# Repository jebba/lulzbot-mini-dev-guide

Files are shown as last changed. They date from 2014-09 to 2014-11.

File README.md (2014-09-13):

# LulzBot Mini Developers Guide

[LulzBot Mini Developers Guide PDF](mini-dev.pdf)

The [LulzBot Mini](http://devel.lulzbot.com/mini/) is a Desktop 3D Printer
currently under development by
[Aleph Objects, Inc.](http://www.alephobjects.com/)

This guide is meant for developers working on the printer or others interested
in learning more about how the machine operates.

Users should see the separate (forthcoming) LulzBot Mini User Manual.

The Guide is written in LaTeX.

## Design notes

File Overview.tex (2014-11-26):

%
% Introduction.tex
%
% LulzBot Mini Developer's Guide
%
% Copyright (C) 2014 Aleph Objects, Inc.
%
% This document is licensed under the Creative Commons Attribution 4.0
% International Public License (CC BY-SA 4.0) by Aleph Objects, Inc.
%

\section{LulzBot Mini}
The LulzBot Mini is a 3D Printer currently under development. The
abbreviated name is mini-dev.

The source files are available here:

\href{http://devel.lulzbot.com/mini/}{http://devel.lulzbot.com/mini/}

\section{Versions}
Each new version of the mini-dev has a new name, with the next letter in the alphabet.

\begin{itemize}
  \item Azalea - First Prototype
  \item Begonia - Second Prototype, being built now
  \item Camellia - Third Prototype
  \item Croton - Fourth Prototype
  \item Daffodil - First Production batch
\end{itemize}

\section{Schedule}
The schedule is updated weekly. It is in Libre Office spreadsheet format. The
latest version is available here:

\url{http://devel.lulzbot.com/mini/program_management/}

\includepdf[addtolist={1,figure,{Work Breakdown Schedule},wbs},pages=-,landscape=true,reflect=false,turn=true,fitpaper=true,keepaspectratio=true]{pm/wbs30.pdf}

\includepdf[addtolist={1,figure,{Phase Gate Schedule},pgs},pages=-,landscape=true,reflect=false,turn=true,fitpaper=true,keepaspectratio=true]{pm/phase-gate-schedule31.pdf}

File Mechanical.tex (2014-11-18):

%
% Mechanical.tex
% Mechanical Development
%
% LulzBot Mini Developer's Guide
%
% Copyright (C) 2014 Aleph Objects, Inc.
%
% This document is licensed under the Creative Commons Attribution 4.0
% International Public License (CC BY-SA 4.0) by Aleph Objects, Inc.
%

\section{Intro}
Mechanical hardware specs and parts are in these subdirectories:

\url{http://devel.lulzbot.com/mini/}

\section{Bill of Materials}

% pdfjam  --papersize '{24.58cm,18.90cm}'   --no-landscape daffodil_bom.pdf '1-3'
\includepdf[addtolist={1,figure,{Bill of Materials},bom},pages=-,landscape=true,reflect=false,turn=false,fitpaper=true,keepaspectratio=true]{bom.pdf}

\section{Drawings}
\includepdf[addtolist={1,figure,{Electronics Case},eleccase},pages=-,landscape=true,reflect=false,turn=false,fitpaper=true,keepaspectratio=true]{PP-FP0056rC.pdf}
\includepdf[addtolist={1,figure,{Top Plate},topplate},pages=-,landscape=true,reflect=false,turn=false,fitpaper=true,keepaspectratio=true]{PP-FP0051rA.pdf}
\includepdf[addtolist={1,figure,{Bottom Plate},bottomplate},pages=-,landscape=true,reflect=false,turn=false,fitpaper=true,keepaspectratio=true]{PP-FP0053rA.pdf}
\includepdf[addtolist={1,figure,{Left Plate},leftplate},pages=-,landscape=true,reflect=false,turn=false,fitpaper=true,keepaspectratio=true]{PP-FP0055rB.pdf}
\includepdf[addtolist={1,figure,{Right Plate},rightplate},pages=-,landscape=true,reflect=false,turn=false,fitpaper=true,keepaspectratio=true]{PP-FP0052rA.pdf}
\includepdf[addtolist={1,figure,{Bed Mount Plate},bedmountplate},pages=-,landscape=true,reflect=false,turn=false,fitpaper=true,keepaspectratio=true]{PP-FP0054rA.pdf}
\includepdf[addtolist={1,figure,{Drive Rod 10mm},drvrod},pages=-,landscape=true,reflect=false,turn=false,fitpaper=true,keepaspectratio=true]{driverod10mm.pdf}

\section{3D Printed Parts}
% PNGs were created thusly:
% Open STL in FreeCAD
% View-->Standard View-->Fit All
% Then hit 0 (zero) for axometric view
% Tools-->Save Picture
% XXX DO NOT USE UNDERSCORES (_) IN THE FILENAME!!! XXX

\section{Bed}
\begin{figure}[H]
\centering
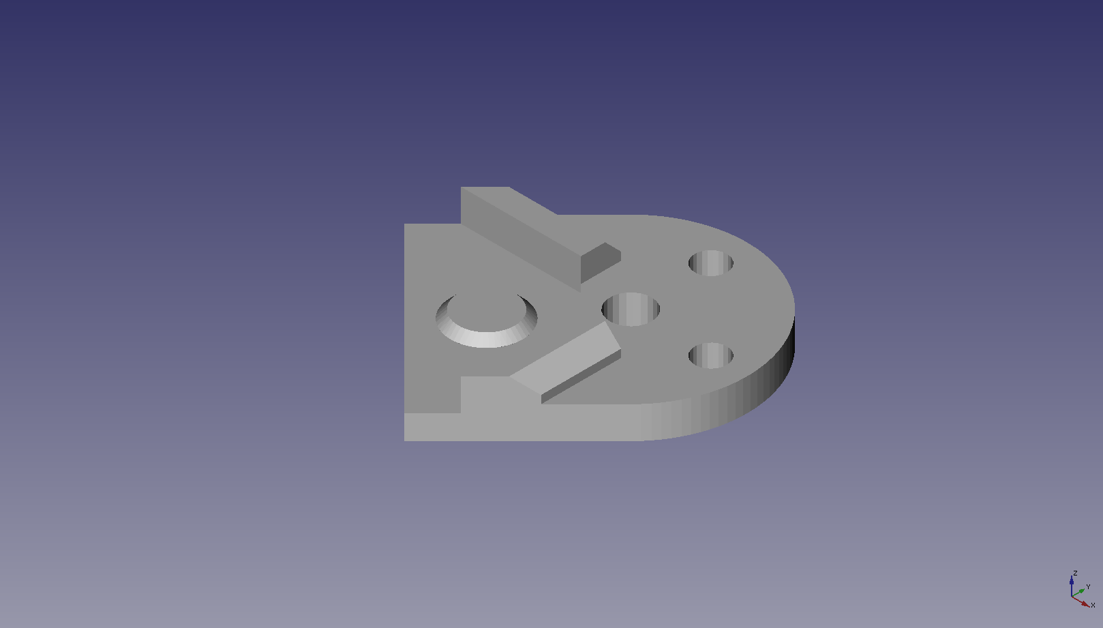
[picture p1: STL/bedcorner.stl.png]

\caption{3D Printed Bed Corner Render}
\label{fig:bedcornerrender}
\end{figure}

\section{Extruder}
\begin{figure}[H]
\centering
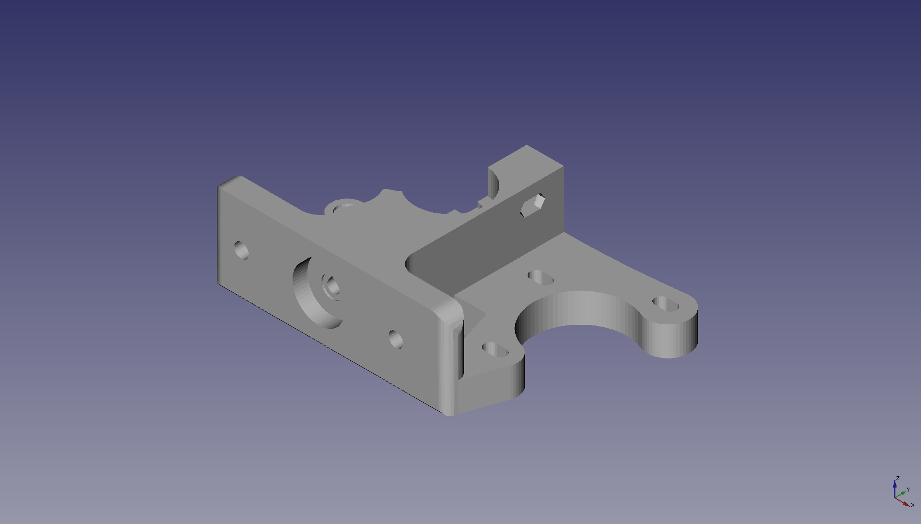
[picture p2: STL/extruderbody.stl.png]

\caption{3D Printed Extruder Body Render}
\label{fig:extruderbodyrender}
\end{figure}

\begin{figure}[H]
\centering
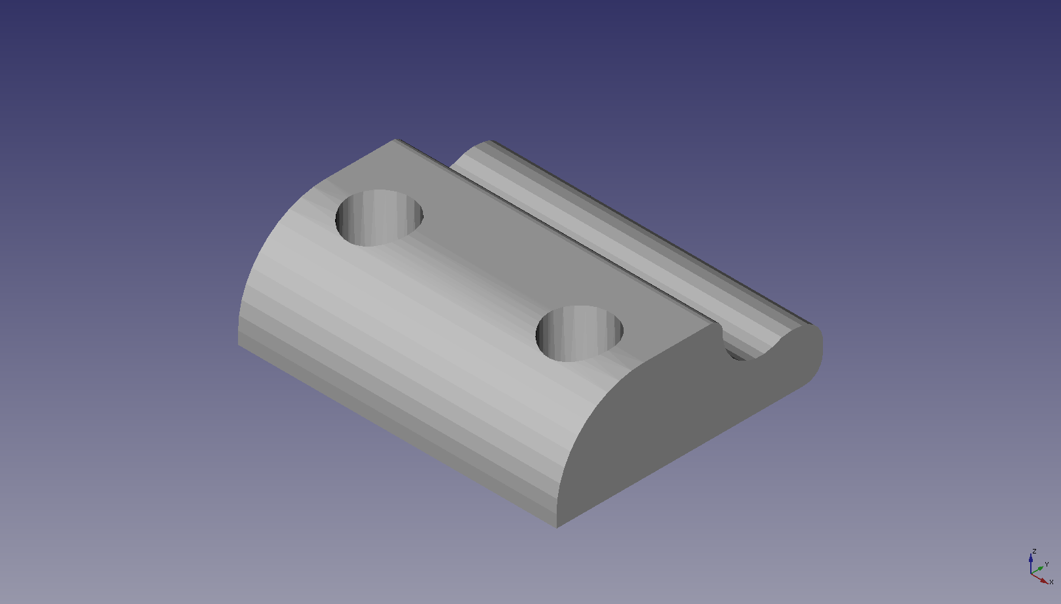
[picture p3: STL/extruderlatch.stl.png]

\caption{3D Printed Extruder Latch Render}
\label{fig:extruderlatchrender}
\end{figure}

\begin{figure}[H]
\centering
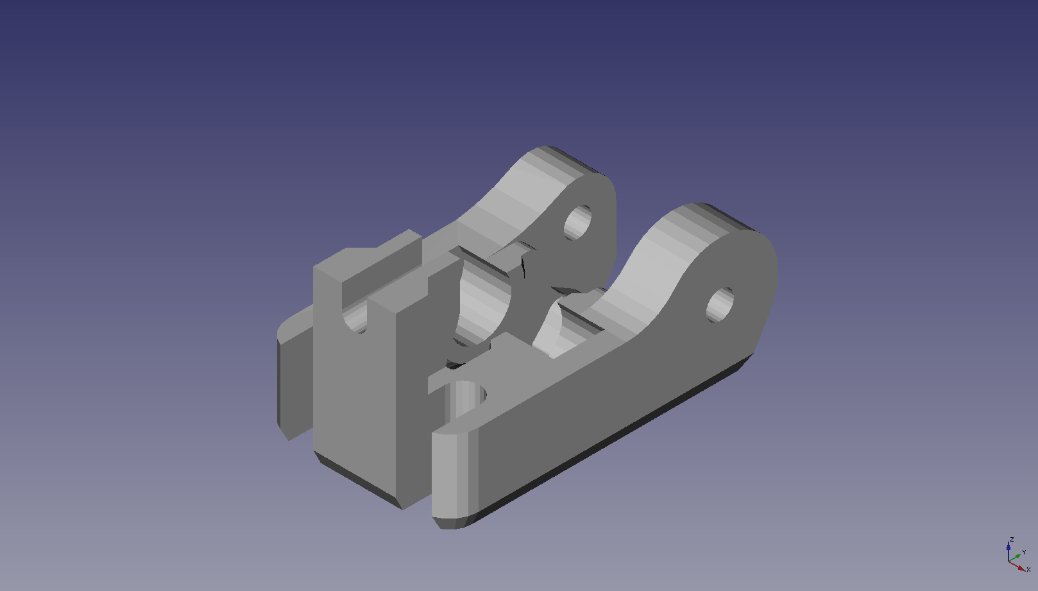
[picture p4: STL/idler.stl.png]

\caption{3D Printed Idler Render}
\label{fig:idlerrender}
\end{figure}

\begin{figure}[H]
\centering
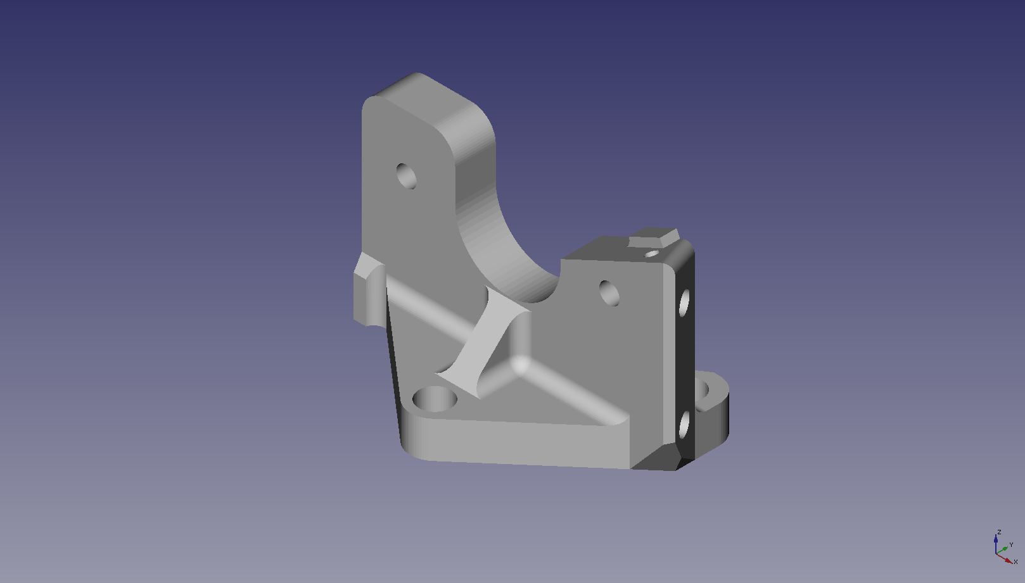
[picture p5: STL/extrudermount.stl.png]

\caption{3D Printed Extruder Mount Render}
\label{fig:extrudermountrender}
\end{figure}

\begin{figure}[H]
\centering
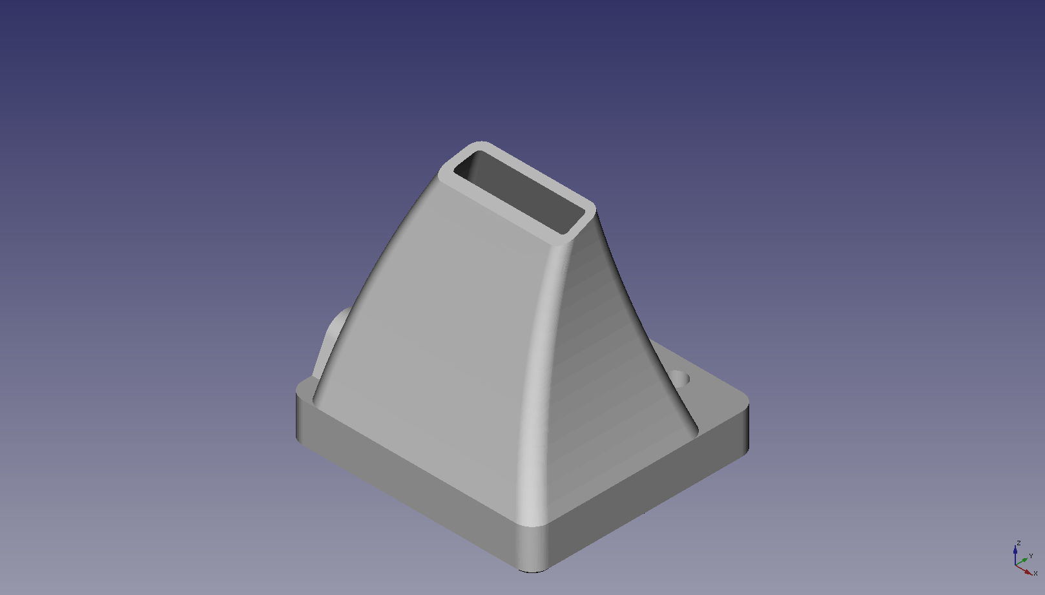
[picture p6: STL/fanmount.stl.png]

\caption{3D Printed Fan Mount Render}
\label{fig:fanmountrender}
\end{figure}

\begin{figure}[H]
\centering
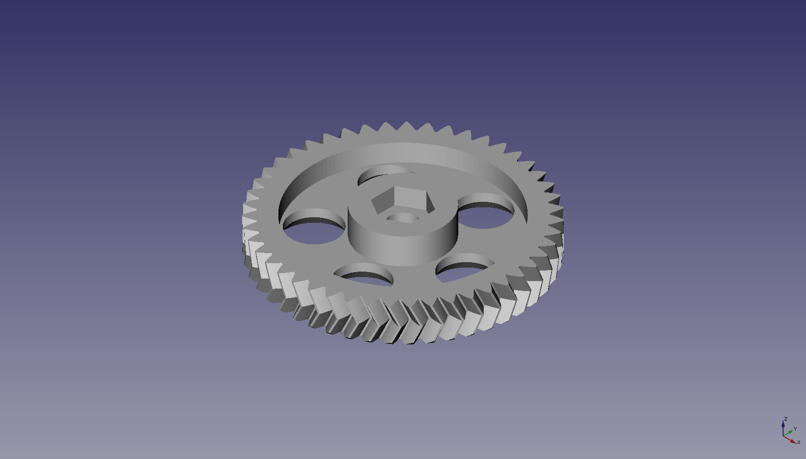
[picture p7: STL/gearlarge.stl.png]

\caption{3D Printed Large Gear Render}
\label{fig:gearlargerender}
\end{figure}

\begin{figure}[H]
\centering
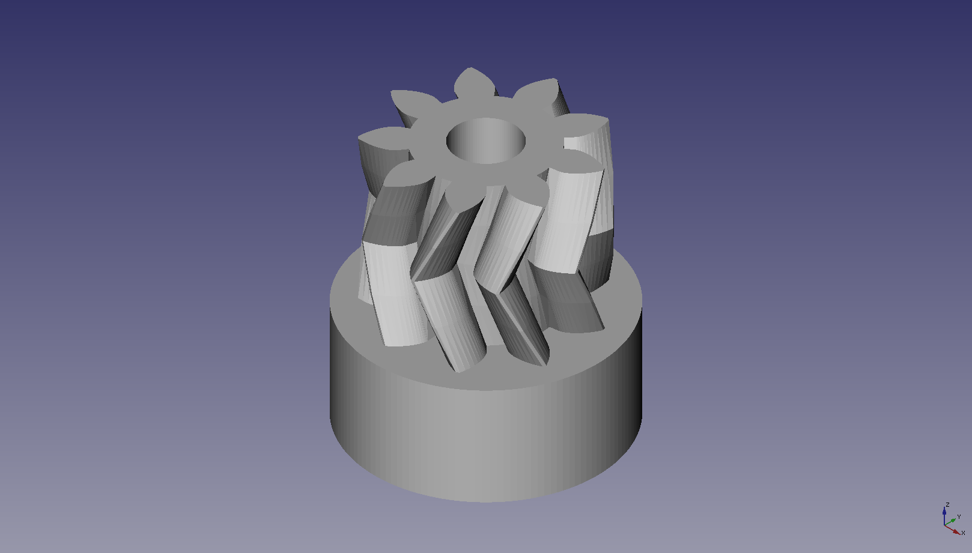
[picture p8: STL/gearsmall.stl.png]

\caption{3D Printed Small Gear Render}
\label{fig:gearsmallrender}
\end{figure}

\section{Spool}

\begin{figure}[H]
\centering
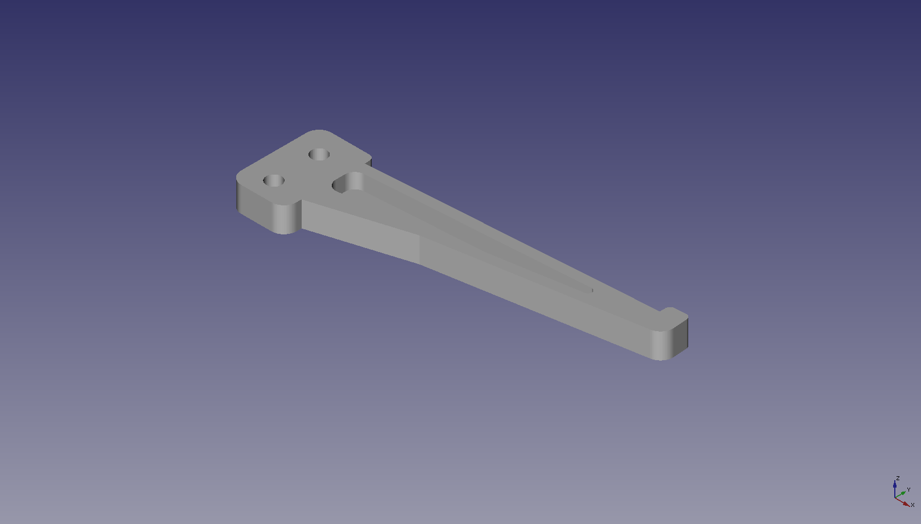
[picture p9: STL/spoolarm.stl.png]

\caption{3D Printed Spool Arm Render}
\label{fig:spoolarmrender}
\end{figure}

\begin{figure}[H]
\centering
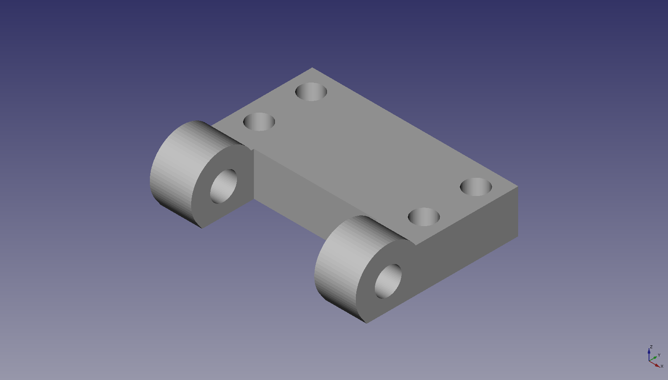
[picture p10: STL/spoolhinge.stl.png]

\caption{3D Printed Spool Hinge Render}
\label{fig:spoolhingerender}
\end{figure}

\begin{figure}[H]
\centering
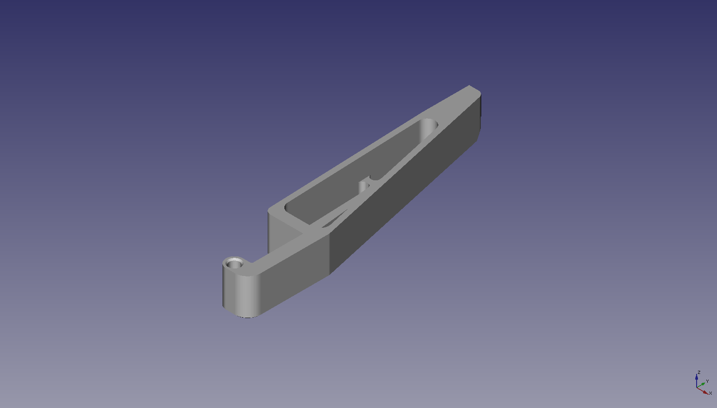
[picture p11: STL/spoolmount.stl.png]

\caption{3D Printed Spool Mount Render}
\label{fig:spoolmountrender}
\end{figure}

\section{X}

\begin{figure}[H]
\centering
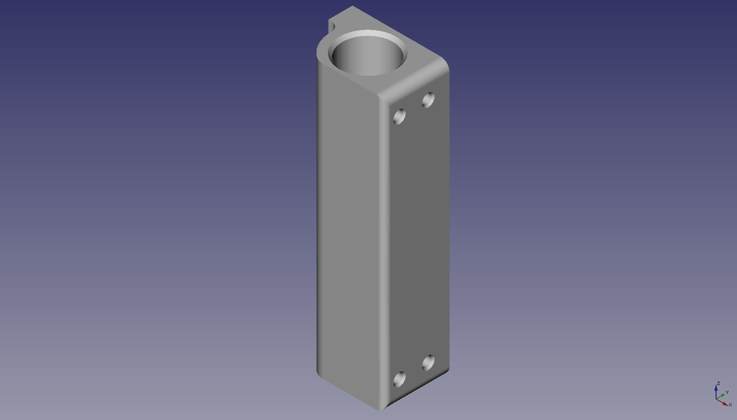
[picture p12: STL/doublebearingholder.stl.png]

\caption{3D Printed Double Bearing Holder Render}
\label{fig:doublebearingholderrender}
\end{figure}

\begin{figure}[H]
\centering
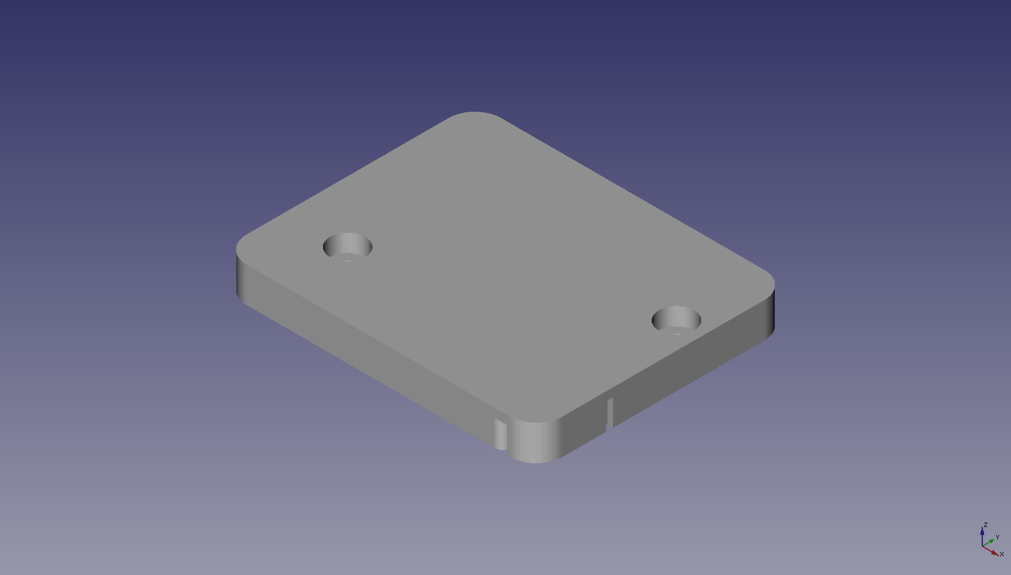
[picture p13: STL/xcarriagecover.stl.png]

\caption{3D Printed X Carriage Cover Render}
\label{fig:xcarriagecoverrender}
\end{figure}

\begin{figure}[H]
\centering
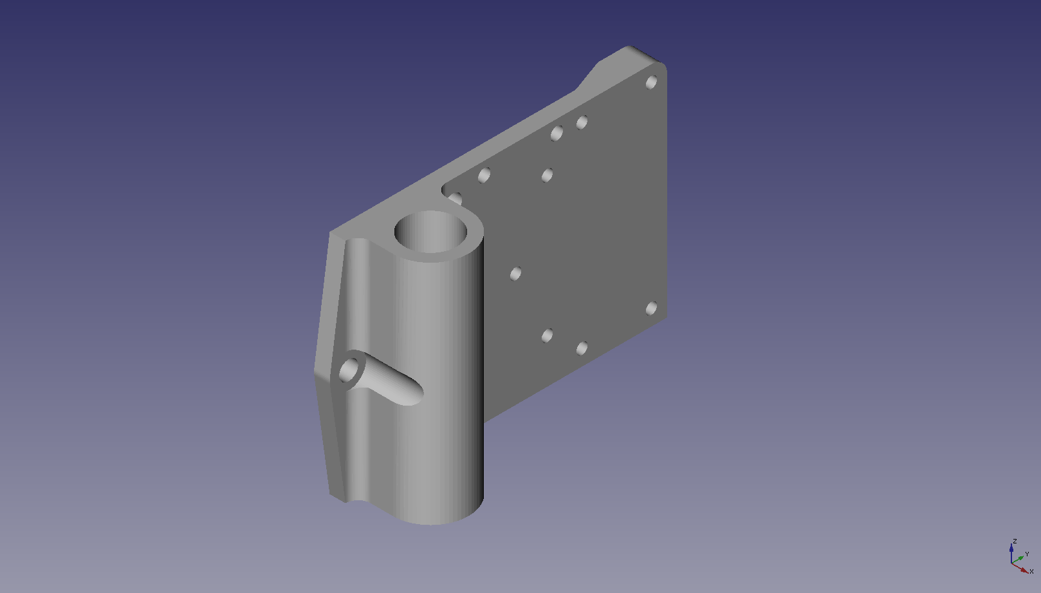
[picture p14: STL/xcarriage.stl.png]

\caption{3D Printed X Carriage Render}
\label{fig:xcarriagerender}
\end{figure}

\begin{figure}[H]
\centering
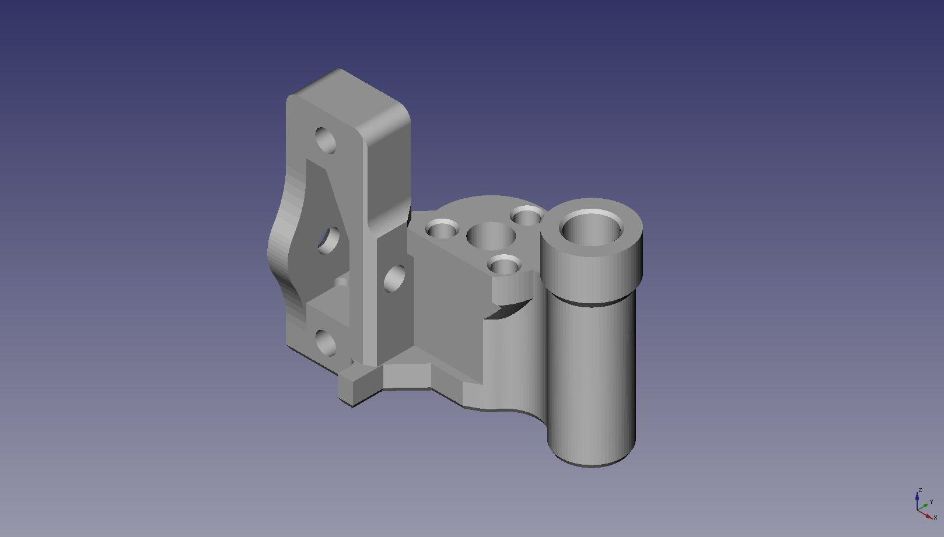
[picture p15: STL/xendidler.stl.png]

\caption{3D Printed X End Idler Render}
\label{fig:xendidlerrender}
\end{figure}

\begin{figure}[H]
\centering
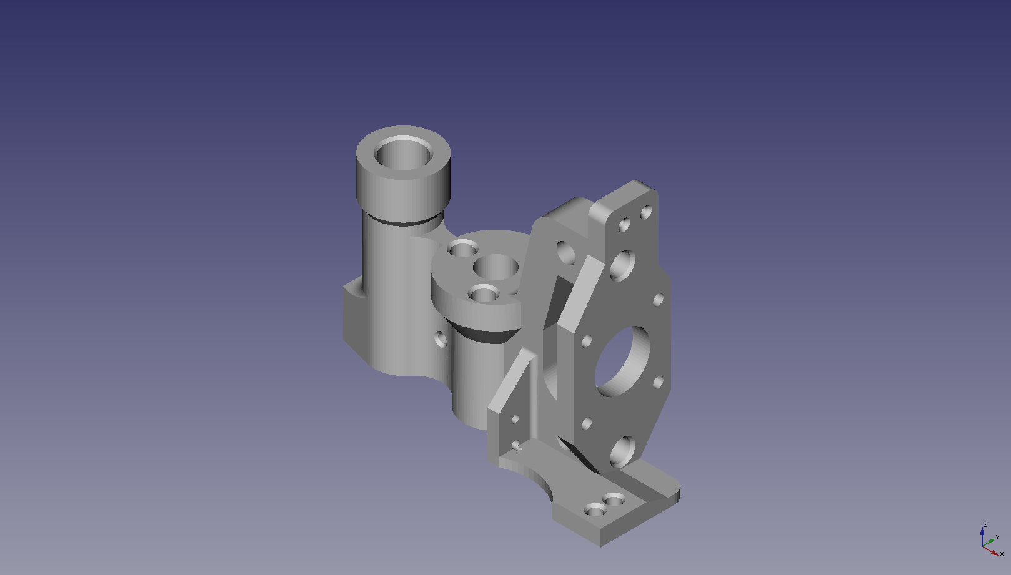
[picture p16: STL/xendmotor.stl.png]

\caption{3D Printed X End Motor Render}
\label{fig:render}
\end{figure}

\section{Y}

\begin{figure}[H]
\centering
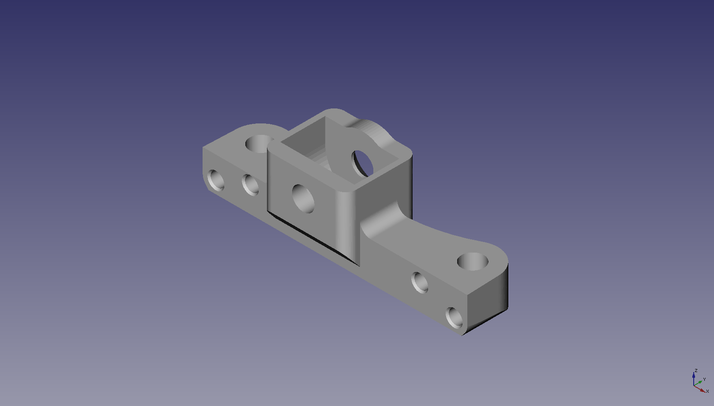
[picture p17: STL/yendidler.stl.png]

\caption{3D Printed Y End Idler Render}
\label{fig:render}
\end{figure}

\begin{figure}[H]
\centering
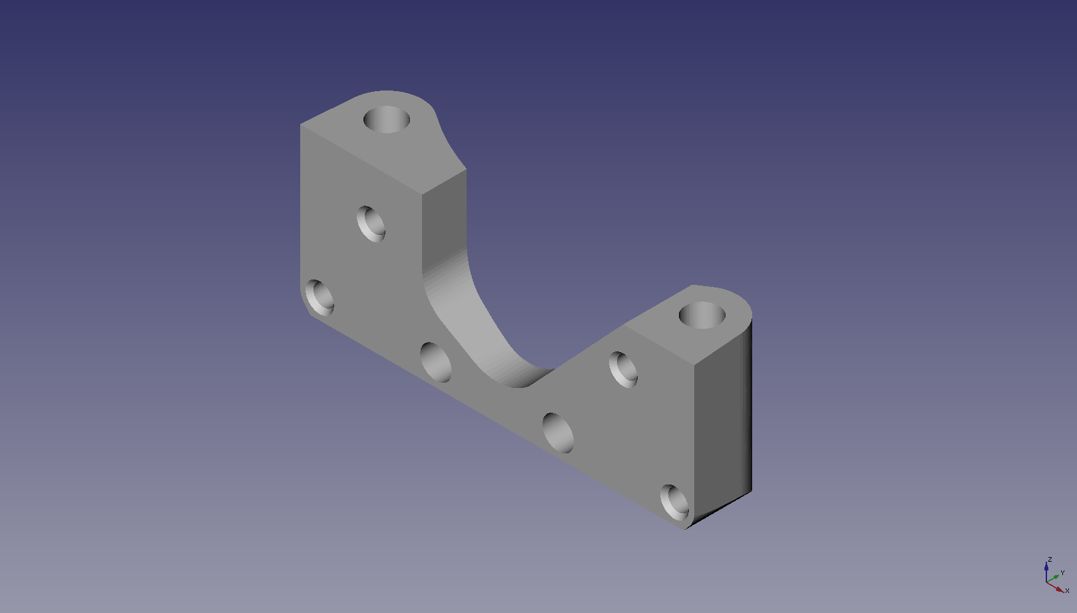
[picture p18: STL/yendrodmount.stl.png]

\caption{3D Printed Y End Rod Mount Render}
\label{fig:yendrodmountrender}
\end{figure}

\section{Z}

\begin{figure}[H]
\centering
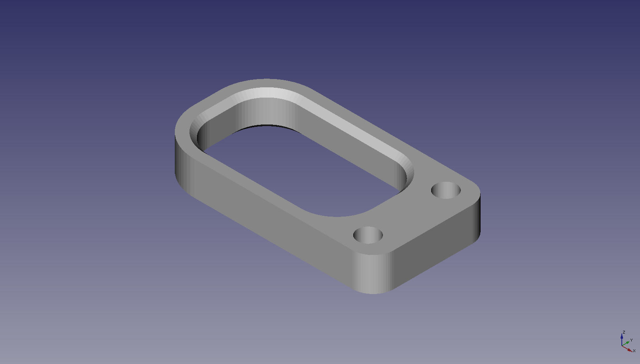
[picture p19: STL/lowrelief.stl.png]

\caption{3D Printed Lower Relief Render}
\label{fig:lowreliefrender}
\end{figure}

\begin{figure}[H]
\centering
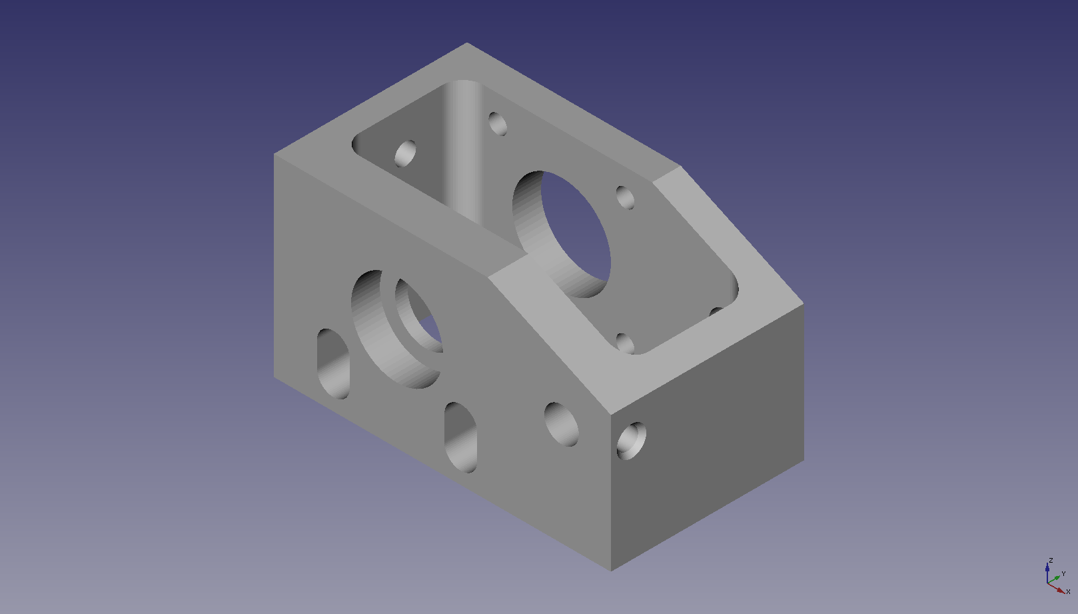
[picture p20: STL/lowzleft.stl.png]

\caption{3D Printed Lower Z Left Render}
\label{fig:lowzleftrender}
\end{figure}

\begin{figure}[H]
\centering
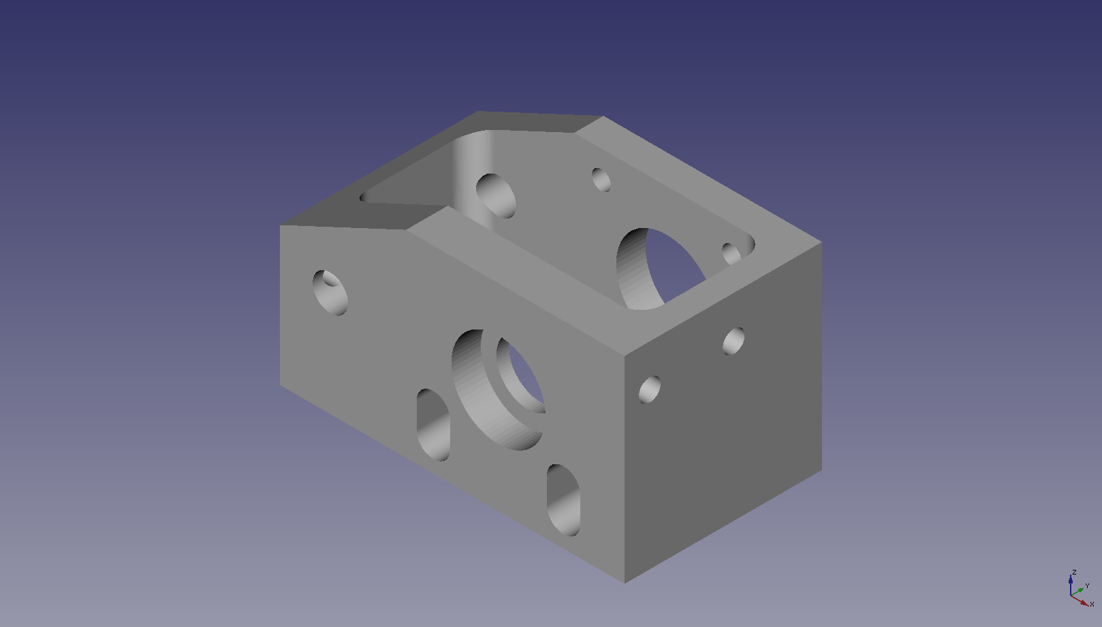
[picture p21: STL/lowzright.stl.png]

\caption{3D Printed Lower Z Right Render}
\label{fig:lowzrightrender}
\end{figure}

\begin{figure}[H]
\centering
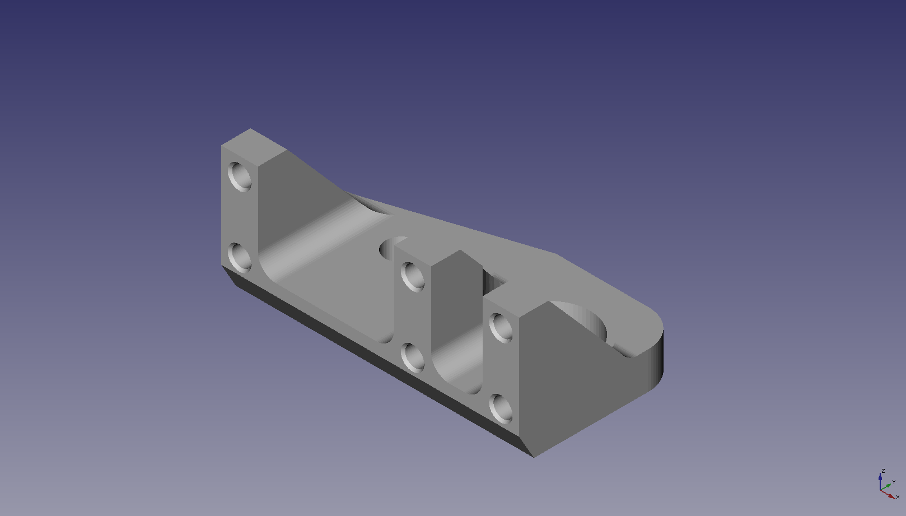
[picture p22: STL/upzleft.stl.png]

\caption{3D Printed Upper Z Left Render}
\label{fig:upzleftrender}
\end{figure}

\begin{figure}[H]
\centering
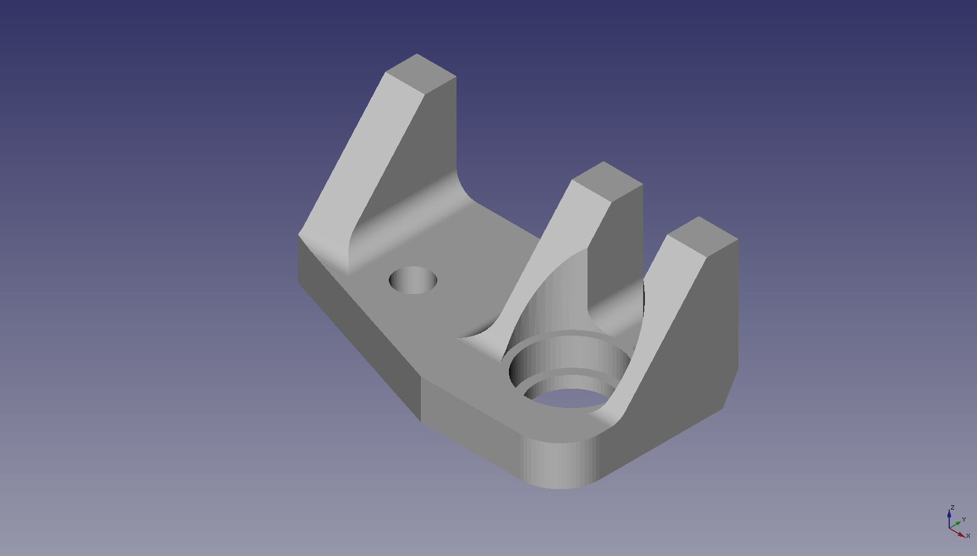
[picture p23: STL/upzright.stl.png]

\caption{3D Printed Upper Z Right Render}
\label{fig:upzrightrender}
\end{figure}

\section{Misc}

\begin{figure}[H]
\centering
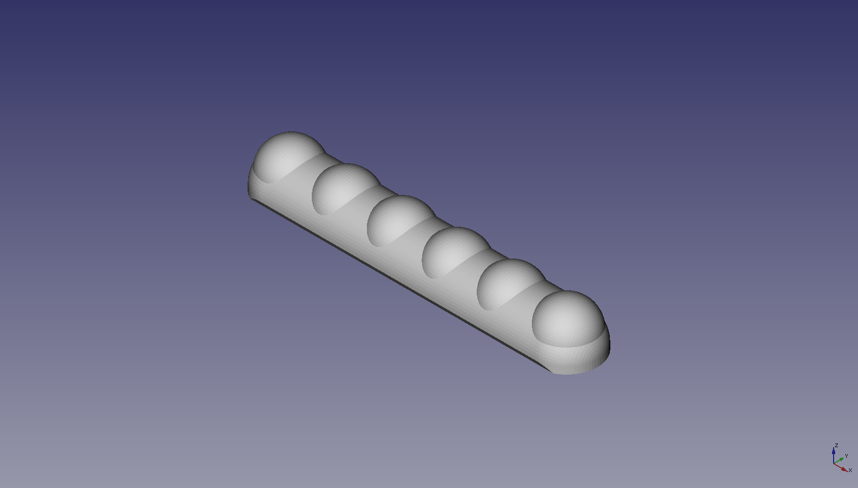
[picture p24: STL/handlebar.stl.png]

\caption{3D Printed Handle Bar Render}
\label{fig:handlebarrender}
\end{figure}

\begin{figure}[H]
\centering

\caption{3D Printed Relief Mount Render}
\label{fig:reliefmountrender}
\end{figure}

\begin{figure}[H]
\centering

\caption{3D Printed Upper Bearing Holder Render}
\label{fig:upperbearingholderrender}
\end{figure}

\begin{figure}[H]
\centering

\caption{3D Printed Wiper Mount Render}
\label{fig:wipermountrender}
\end{figure}

\begin{figure}[H]
\centering

\caption{3D Printed Belt Mount Render}
\label{fig:beltmountrender}
\end{figure}

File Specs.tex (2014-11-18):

%
% Specs.tex
% Specs Development
%
% LulzBot Mini Developer's Guide
%
% Copyright (C) 2014 Aleph Objects, Inc.
%
% This document is licensed under the Creative Commons Attribution 4.0
% International Public License (CC BY-SA 4.0) by Aleph Objects, Inc.
%

\section{Specifications}

\subsection{Printing}
\begin{itemize}
\item Print Surface: Heated Borosilicate glass bed covered with PEI film
\item Print Area:155mm x 155mm x 155mm (6.1in x 6.1in x 6.1in)
\item Print Volume: 3,726cm3 (227.4 in3) of usable space
\item Top Print Speed: 275mm/sec (10.8in/sec)
\item Print Tolerance: 0.1mm (0.0039in) in X and Y axes. Z axis is dependent on layer thickness
\item Layer Thickness: 0.075mm to 0.50mm (0.003in - 0.020in)
\item Supported Materials: ABS, PLA, HIPS, PVA, wood filled filaments, Polyester (Tritan), PETT, filled PLA, Bronze and copper filled filaments, Polycarbonate, Nylon, PETG, Conductive PLA and ABS, UV luminescent filaments, PCTPE, PC-ABS, and more every day.
\item Usable Filament Sizes: standard 3mm (0.1in)
\end{itemize}
\subsection{Phyiscal Dimensions}
\begin{itemize}
\item Overall Dimensions: 435mm x 340mm x 385mm (17.1in x 13.4in x 15.2in)
\item Weight: 8.55kg (18.85lbs)
\end{itemize}
\subsection{Electrical}
\begin{itemize}
\item Power Requirements: 100 - 240 VAC
\item Power Supply: 24V 150W
\item US, UK, and EU electrical plugs available
\end{itemize}
\subsection{Temperature}
\begin{itemize}
\item Temperature: Maximum operating temperature (Extruder), 300C (572F)
\item Temperature: Maximum operating temperature (Heated Bed), 120C (248F)
\end{itemize}

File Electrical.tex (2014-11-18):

%
% Electrical.tex
% Electrical Development
%
% LulzBot Mini Developer's Guide
%
% Copyright (C) 2014 Aleph Objects, Inc.
%
% This document is licensed under the Creative Commons Attribution 4.0
% International Public License (CC BY-SA 4.0) by Aleph Objects, Inc.
%

\section{Electrical Layout}

\includepdf[addtolist={1,figure,{Camillia Electrical Layout},eleclayoutcam},pages=-,landscape=true,reflect=false,turn=true,fitpaper=true,keepaspectratio=true]{camellia_elec_layout.pdf}

\section{Wire Harness List}

\includepdf[addtolist={1,figure,{Wire Harness List},wireharnlist},pages=-,landscape=true,reflect=false,turn=true,fitpaper=true,keepaspectratio=true]{wire-harness-list.pdf}

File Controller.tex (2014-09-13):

%
% Controller.tex
% Mini-RAMBo 3D Printer Controller Electronics Board
%
% LulzBot Mini Developer's Guide
%
% Copyright (C) 2014 Aleph Objects, Inc.
%
% This document is licensed under the Creative Commons Attribution 4.0
% International Public License (CC BY-SA 4.0) by Aleph Objects, Inc.
%

\section{Intro}
The printer controller will be the RAMBo-Mini.

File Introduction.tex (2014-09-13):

%
% Introduction.tex
%
% LulzBot Mini Developer's Guide
%
% Copyright (C) 2014 Aleph Objects, Inc.
%
% This document is licensed under the Creative Commons Attribution 4.0
% International Public License (CC BY-SA 4.0) by Aleph Objects, Inc.
%

\section{Audience}
This is a developer's guide to hacking on the LulzBot Mini 3D Printer.
It is meant for developers, not users, of the printer.

\section{Open Source Hardware, Free Software}

Aleph Objects, Inc. is a Loveland, Colorado, USA company that manufactures
Open Source Hardware using Free Software.

For more info, visit \url{http://www.alephobjects.com}.

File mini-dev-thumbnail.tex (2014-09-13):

%
% mini-dev-thumbnail.tex
% Create thumbnail images of PDF pages
%
% LulzBot Mini Developer's Guide
%
% Copyright (C) 2014 Aleph Objects, Inc.
%
% This document is licensed under the Creative Commons Attribution 4.0
% International Public License (CC BY-SA 4.0) by Aleph Objects, Inc.
%

\documentclass[twoside]{minimal}
\usepackage[paperwidth=22.86cm, paperheight=30.48cm,dvips=false,pdftex=false,vtex=false]{geometry}
\usepackage[final]{pdfpages}
\usepackage{pdflscape}
\usepackage{thumbpdf}
\begin{document}
\includepdf[nup=2x4,pages={{},-},landscape]{mini-dev.pdf}
\end{document}

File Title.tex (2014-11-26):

%
% Title.tex
%
% LulzBot Mini Developer's Guide
%
% Copyright (C) 2014 Aleph Objects, Inc.
%
% This document is licensed under the Creative Commons Attribution 4.0
% International Public License (CC BY-SA 4.0) by Aleph Objects, Inc.
%

\date {}
\thispagestyle{empty}
\begin{center}
\par


{\fontspec{Outage.ttf}\fontsize{25pt}{5cm}\selectfont \textcolor{ao-purple}{LulzBot Mini Developer's Guide}}



\end{center}

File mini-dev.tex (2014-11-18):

%
% mini-dev.tex
% Main LaTeX document for formatting mini-dev
%
% LulzBot Mini Developer's Guide
%
% Copyright (C) 2014 Aleph Objects, Inc.
%
% This document is licensed under the Creative Commons Attribution 4.0
% International Public License (CC BY-SA 4.0) by Aleph Objects, Inc.
%

%%% XXX NOTE

%%% Glossaries and indices are broken:
%%% https://sharelatex.tenderapp.com/help/discussions/questions/19378-glossaries-indices-and-speed

%%% XXX NOTE

% LaTeX Docs:
% http://en.wikibooks.org/wiki/Category:LaTeX

% LaTeX Memoir Class
% Docs: /usr/share/doc/texlive-latex-recommended-doc/latex/memoir/memman.pdf
\documentclass[twoside,12pt,openright,final,english]{memoir}

\usepackage{tikz}
\usetikzlibrary{shadows,shapes,arrows,chains,calc,decorations.pathmorphing,patterns,trees,positioning,automata,fit}
% This breaks things, but would be great to use
%\usepackage{tikz-qtree,tikz-qtree-compat}
\usepackage{rotating}
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
\usepackage{epstopdf} % Docs: /usr/share/doc/texlive-doc/latex/oberdiek/epstopdf.pdf
\usepackage[colorlinks=true]{hyperref}
    % Docs: http://en.wikibooks.org/wiki/LaTeX/Hyperlinks
    %       http://www.tug.org/applications/hyperref/manual.html
\graphicspath{{./docs/}{./images/}{./drawings/}}

\makeindex
\makeglossary

\usepackage{color} % Docs: /usr/share/doc/texlive-latex-base-doc/latex/graphics/grfguide.pdf
%\usepackage[usenames,dvipsnames,svgnames,table]{xcolor}

%%% PREAMBLE FONTS %%%
% For XeTeX
% http://www.ctan.org/pkg/fontspec
% http://mirrors.ctan.org/macros/latex/contrib/fontspec/fontspec.pdf
\usepackage{fontspec}
\defaultfontfeatures{Ligatures=TeX} % To support LaTeX quoting style
\setmainfont{lmroman12-regular.otf}

\usepackage[normalem]{ulem} % underline

\usepackage{floatpag} % Full page figures without page numbers.

%%% END PREAMBLE FONTS %%%

%%% PAGE, STOCK, AND MARGIN SIZE %%%
% 7.44 x 9.68"   18.90 x 24.58cm
\setstocksize{24.58cm}{18.90cm} % { height }{ width }
\settrimmedsize{\stockheight}{\stockwidth}{*}

%\settypeblocksize{ height }{ width }{ ratio }
\settypeblocksize{19.0cm}{*}{*}

%\setlrmarginsandblock{ spine }{ edge }{ ratio }
% make the spine have more space than outer edge
\setlrmarginsandblock{*}{2.5cm}{1.2}

% \setulmargins{ upper }{ lower }{ ratio }
\setulmargins{2.0cm}{*}{*}

% \setheadfoot{ headheight }{ footskip }
\setheadfoot{12pt}{2cm}

\checkandfixthelayout[fixed]
%%% END PAGE, STOCK, AND MARGIN SIZE %%%

\setcounter{secnumdepth}{3}
\setcounter{tocdepth}{3}

\usepackage[english]{babel}
\usepackage{datetime} % Docs: /usr/share/doc/texlive-doc/latex/datetime/datetime.pdf
\usepackage{ucs}

%%% PDFLATEX %%%
\usepackage{etex}

%%% Not all features are used in XeTeX
\usepackage[protrusion,babel,final]{microtype}
%%% Conflicts with package fontspec
%\usepackage[utf8x]{inputenc}

% Docs: /usr/share/doc/texlive-humanities-doc/latex/ledmac/ledmac.pdf
%\usepackage{eledmac}

%%% mini-dev PAGE STYLE %%%
\makepagestyle{aoomstyle}
\pagestyle{aoomstyle}
\makeevenhead{aoomstyle}{}{\hspace{2em}\itshape\small\leftmark}{}
\makeoddhead{aoomstyle}{}{\scshape\small\rightmark}{}
\makeevenfoot{aoomstyle}{}{\hspace{2em}\thepage}{}
\makeoddfoot{aoomstyle}{}{\thepage}{}
%%% END mini-dev PAGE STYLE %%%

%%% mini-devSKI CHAPTER STYLE %%%
\makechapterstyle{aoomski}{%
  \renewcommand*{\printchaptername}{}	% Clear out the chapter name (e.g. capítulo)
  \renewcommand*{\printchapternum}{}	% Clear out the chapter number
  \renewcommand*{\chaptitlefont}{\fontspec{Montserrat-Regular.ttf}\fontsize{20pt}{3em}\selectfont}	% Set chapter title font
  \renewcommand*{\printchaptertitle}[1]{%
     \hrule\vskip\onelineskip \centering \chaptitlefont{##1}\par}
  % Set chapter title font
  \renewcommand*{\afterchaptertitle}{\vskip\onelineskip \hrule\vskip
     \afterchapskip}
}
%%% END mini-devSKI CHAPTER STYLE %%%

%%% FORMATTING... %%%
\midsloppy
\setlength{\emergencystretch}{3em}
\tolerance=5000
\hyphenpenalty=500
\setlength{\topskip}{1.6\topskip}
\checkandfixthelayout
\raggedbottom
\widowpenalty=10000
\clubpenalty=10000
%%% END FORMATTING... %%%

%%% FOOTNOTES %%%
% no horizontal rule before footnotes:
\let\oldfootnoterule\footnoterule
\renewcommand*{\footnoterule}{}
\setlength{\footmarkwidth}{3.5em}
%%% END FOOTNOTES %%%

%%% COLORS %%%
%\definecolor{ao-purple}{cmyk}{0.50,0.60,0.00,0.43}  % ???
\definecolor{ao-purple}{cmyk}{0.85 0.90 0.00 0.05}
\definecolor{ao-dark-blue}{cmyk}{0.83 0.24 0.00 0.12}
\definecolor{ao-light-blue}{cmyk}{0.41 0.15 0.00 0.09}
\definecolor{ao-light-orange}{cmyk}{0.00 0.40 0.88 0.03}
\definecolor{ao-dark-orange}{cmyk}{0.00 0.51 0.83 0.11}
\definecolor{ao-gold}{cmyk}{0.00 0.18 0.75 0.00}
\definecolor{ao-greyblack}{cmyk}{0.00 0.11 0.09 0.86}
\definecolor{ao-white}{cmyk}{0.00 0.00 0.00 0.00}
\definecolor{ao-black}{cmyk}{1.00 1.00 1.00 1.00}
%%% END COLORS %%%

%%% DEBUG %%%
%\showoutput
%\typeoutlayout
%\typeoutstandardlayout
%%% END DEBUG %%%

%%% END OF PREAMBLE %%%

\begin{document}

%%% BEGIN FRONT MATTER %%%
\frontmatter

% Set page numbers to lowercase roman numerals, and reset the count to 1 (no *)
\pagenumbering{roman}

%%% TITLE PAGE %%%
% We want the title to be on the right hand page.
% If we pad a page, it gives us two with openright
\include{Title}
%%% END TITLE PAGE

%%% COPYRIGHT PAGE %%%
\include{Copyright}
%%% END COPYRIGHT PAGE %%%

%%% TABLE OF CONTENTS %%%
{\fontspec{Montserrat-Regular.ttf}
\maxtocdepth{subsection}
\settocdepth{subsection}
% space between dots
\renewcommand{\cftchapterdotsep}{15}
% dot symbol (default is period)
\renewcommand{\cftdot}{\textperiodcentered}	% centered period
% Set space between each entry in ToC
\setlength{\cftbeforechapterskip}{5pt}
\tableofcontents*}
%%% END TABLE OF CONTENTS %%%

%%% LIST OF FIGURES %%%
\renewcommand*{\lofheadstart}{\vspace{1cm}}
\clearpage
\listoffigures*
%%% END LIST OF FIGURES %%%

%%% CHAPTER STYLE %%%
\chapterstyle{aoomski} % defined in preamble
\def\topblockvspace{0.11}
%%% END CHAPTER STYLE %%%

%%% CHAPTER CONFIG %%%
\newcommand{\chapterheader}{LulzBot Mini Developer's Guide}
% See \chapterconf below for examples of how this is used.
% value 1 is file to include
% value 2 is title of chapter
% value 3 is sub title of chapter
\newcommand{\chapterconf}[3]{
\chapter{\emph{{#2}}\protect \\
{#3}}
\thispagestyle{empty}
\markboth{#2}{\chapterheader}
{\include{#1}}
}
%%% END CHAPTER CONFIG %%%

%%% FRONTMATTER CHAPTERS %%%
\fontspec{lmroman12-regular.otf}

% Format:
% \chapterconf{Name of file to include}{Title of Chapter}
\chapterconf{Introduction}{Introduction}{Welcome Aboard}
%%% END FRONTMATTER CHAPTERS %%%

%%% END FRONTMATTER %%%

%%% BEGIN MAINMATTER %%%
\mainmatter*

% Set page numbering to arabic, but don't reset numbering (*)
\pagenumbering*{arabic}

%% MAINMATTER CHAPTERS %%%
% Default chapter font
\fontspec{lmroman12-regular.otf}

% Format:
% \chapterconf{Name of file to include}{Title of Chapter}{Subtitle}
% Comment out a line to not render that chapter
\chapterconf{Overview}{LulzBot Mini}{Developer Overview}
\chapterconf{Specs}{Specs}{Specifications}
\chapterconf{Mechanical}{Mechanical}{Cartesian Bot in X, Y, Z}
\chapterconf{Electrical}{Electrical}{Power Supply, wiring}
\chapterconf{Controller}{3D Printer Controller}{Mini-RAMBo}
\chapterconf{QA}{Quality Assurance}{Quality Assurance}
\chapterconf{Packing}{Packing}{If It Shakes It Breaks}
\chapterconf{Contact}{Contact}{Phone, Email, Web, Location}
%% END MAINMATTER CHAPTERS %%%

%%% END MAINMATTER %%%

%%% BEGIN BACKMATTER %%%
\backmatter

%%% INDEX %%%
\clearpage
\printindex
%%% END INDEX %%%

%%% GLOSSARY %%%
\renewcommand{\memgloterm}[1]{\textbf{#1}}
\renewcommand{\memglodesc}[1]{\textit{#1}}
\renewcommand{\memglonum}[1]{}

\clearpage
\printglossary
%%% END GLOSSARY %%%

%%% COLOPHON %%%
%%% skip a couple pages
\pagebreak{}
\thispagestyle{empty}
\begingroup 
\vfill\null 
\endgroup
\pagebreak{}
\thispagestyle{empty}
\fontspec{Montserrat-Regular.ttf}
{\include{Colophon}}
%%% END COLOPHON %%%

%%% END BACKMATTER %%%

\end{document}

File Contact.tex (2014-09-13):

%
% Contact.tex
%
% LulzBot Mini Developer's Guide
%
% Copyright (C) 2014 Aleph Objects, Inc.
%
% This document is licensed under the Creative Commons Attribution 4.0
% International Public License (CC BY-SA 4.0) by Aleph Objects, Inc.
%

\section{Support}
\setlength{\parindent}{0pt}
Email: \texttt{support@alephobjects.com}

Phone: +1-970-377-1111 x610

LulzBot Forum

\url{http://forum.lulzbot.com}

\section{Sales}

Email: \texttt{sales@alephobjects.com}

Phone: +1-970-377-1111 x600

\section{Websites}

Aleph Objects, Inc.

\url{http://www.alephobjects.com}

LulzBot 3D Printers

\url{http://www.lulzbot.com}

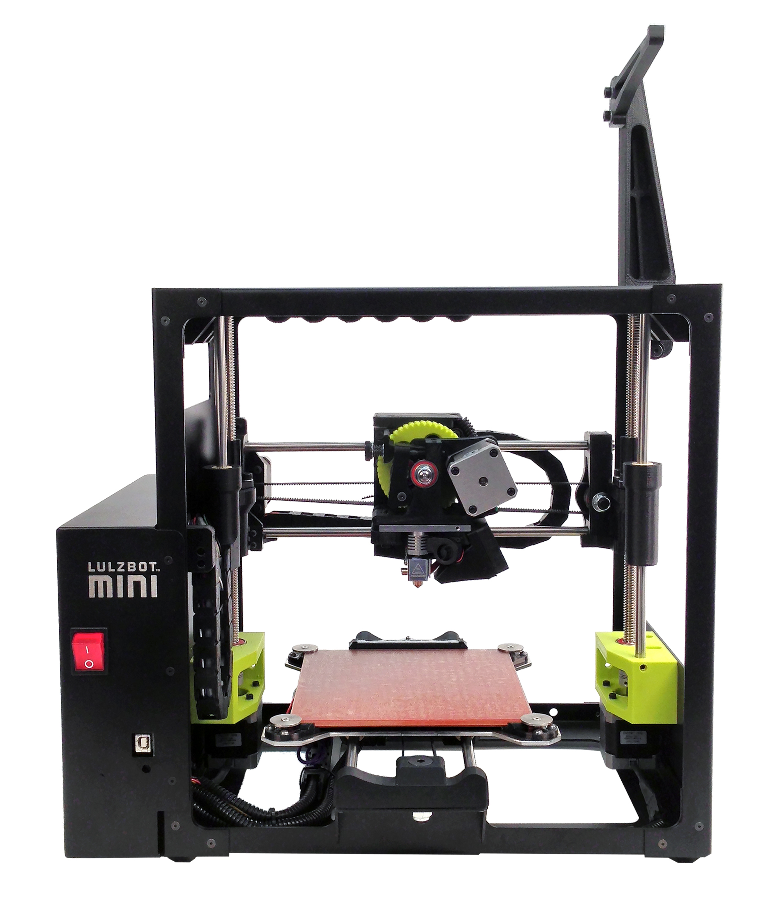
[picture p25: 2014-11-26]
images/croton/Mini_Croton_1.jpg

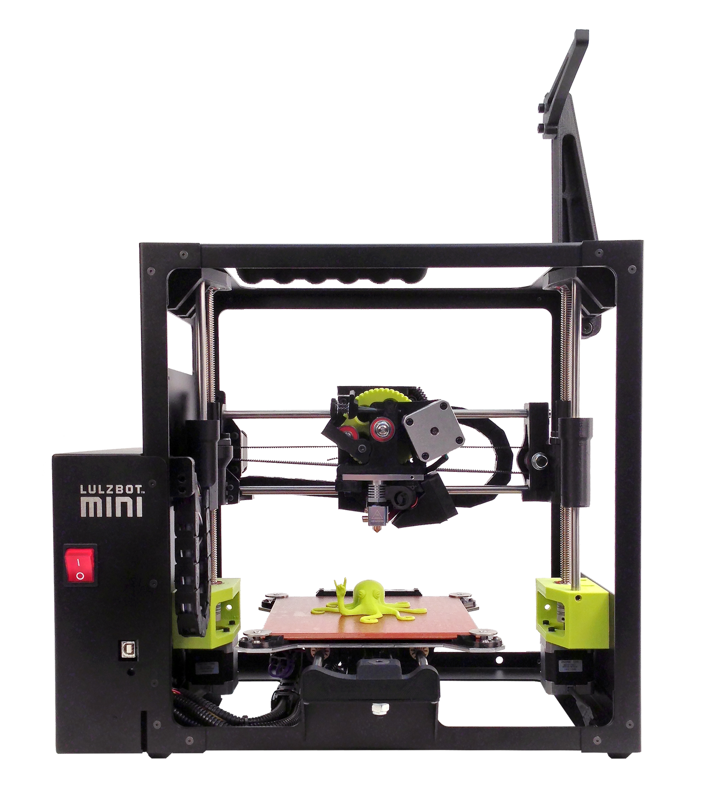
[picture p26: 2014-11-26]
images/croton/Mini_Croton_2.png

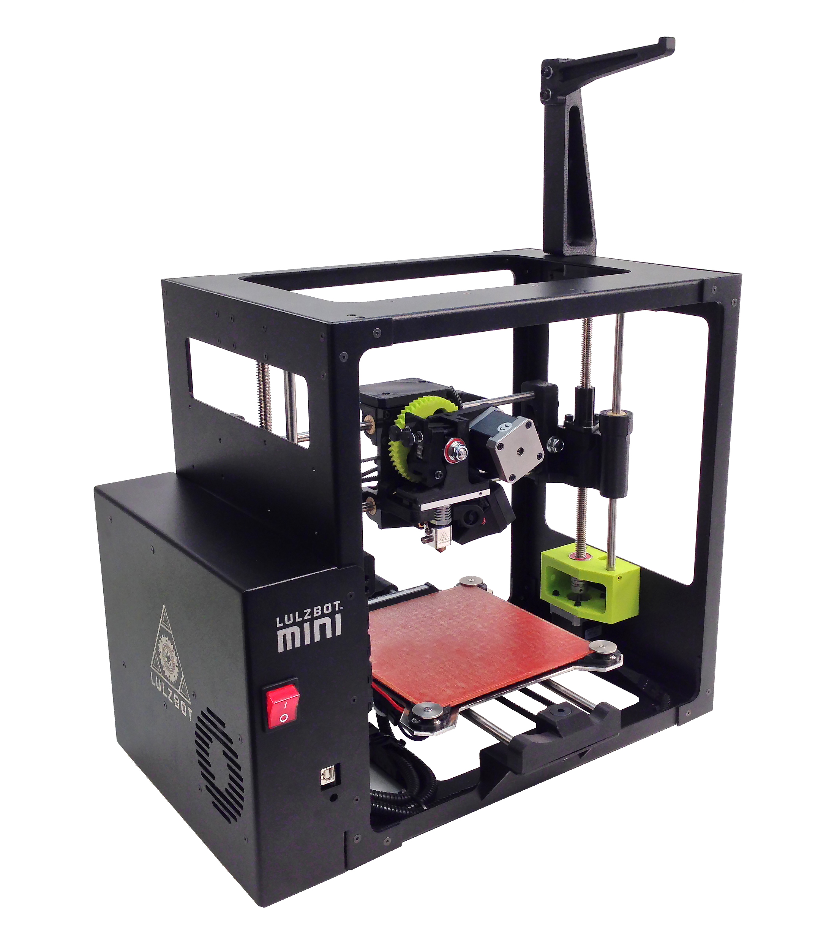
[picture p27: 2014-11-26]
images/croton/Mini_Croton_3.jpg

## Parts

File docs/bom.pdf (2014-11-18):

Category | AO Part # | Description | Manufacturer Manufacturer PN | Distributor | Distributor SKU | Qty Per | UOM Price Per Unit Price Total | Qty to Order
Hardware | HD-MS0054 | Square Bumper | | | Advanced Antivibration co | | 4 | ea | $0.09 | $0.35 | 42 Sheets of 98
Printed | PP-GP0189 | Double bearing holder v1.2, Mini | | | Aleph Objects | | 2 | ea | $3.010 | $6.02
Printed | PP-GP0188 | Upper bearing holder v1.1, Mini | | | Aleph Objects | | 1 | ea | $3.300 | $3.30
Printed | PP-GP0187 | X carriage cover v2.3, Mini | | | Aleph Objects | | 1 | ea | $1.750 | $1.75
Printed | PP-GP0191 | Herringbone Large Gear, Lulzbot green | | | Aleph Objects | | 1 | ea | $2.230 | $2.23
Printed | PP-GP0192 | Herringbone Small Gear, Lulzbot green | | | Aleph Objects | | 1 | ea | $0.290 | $0.29
Printed | PP-GP0060 | Wade Reloaded Bearing Washer | | | Aleph Objects | | 1 | ea | $0.020 | $0.02
Printed | PP-GP0186 | Wade extruder body for Hex nozzle v1.0 | | | Aleph Objects | | 1 | ea | $3.790 | $3.79
Printed | PP-GP0059 | Wade Reloaded Idler Block | | | Aleph Objects | | 1 | ea | $0.900 | $0.90
Printed | PP-GP0091 | extruder_latch | | | Aleph Objects | | 1 | ea | $0.260 | $0.26
Printed | PP-GP0185 | X end idler v2.3, Mini | | | Aleph Objects | | 1 | ea | $7.870 | $7.87
Printed | PP-GP0184 | Extruder mount v2.4, Mini | | | Aleph Objects | | 1 | ea | $3.690 | $3.69
Printed | PP-GP0183 | X carriage v1.0, Mini | | | Aleph Objects | | 1 | ea | $5.150 | $5.15
Printed | PP-GP0182 | X end motor v1.6, Mini | | | Aleph Objects | | 1 | ea | $8.740 | $8.74
Printed | PP-GP0181 | Belt mount v1.0, Mini | | | Aleph Objects | | 2 | ea | $1.260 | $2.52
Printed | PP-GP0179 | Z upper left v1.2, Mini | | | Aleph Objects | | 1 | ea | $3.010 | $3.01
Printed | PP-GP0180 | Z upper right v1.2, Mini | | | Aleph Objects | | 1 | ea | $3.010 | $3.01
Printed | PP-GP0177 | Z lower left v1.1, Mini, Lulzbot green | | | Aleph Objects | | 1 | ea | $5.150 | $5.15
Printed | PP-GP0178 | Z lower right v1.1, Mini, Lulzbot green | | | Aleph Objects | | 1 | ea | $5.150 | $5.15
Printed | PP-GP0176 | Bed corner v2.2, Mini | | | Aleph Objects | | 4 | ea | $0.290 | $1.16
Printed | PP-GP0175 | Y idler mount v1.2, Mini | | | Aleph Objects | | 1 | ea | $2.230 | $2.23
Printed | PP-GP0174 | Y rod mount v1.1, Mini | | | Aleph Objects | | 1 | ea | $3.010 | $3.01
Printed | PP-GP0173 | Spool hinge v1.3, Mini | | | Aleph Objects | | 1 | ea | $0.870 | $0.87
Printed | PP-GP0172 | Spool arm v1.0, Mini | | | Aleph Objects | | 1 | ea | $1.550 | $1.55
Printed | PP-GP0171 | Spool mount v1.2, Mini | | | Aleph Objects | | 1 | ea | $7.090 | $7.09
Printed | PP-GP0170 | Relief mount v1.3, Mini | | | Aleph Objects | | 1 | ea | $1.070 | $1.07
Printed | PP-GP0169 | Handle bar v2.4, Mini | | | Aleph Objects | | 1 | ea | $2.040 | $2.04
Printed | PP-GP0168 | Wiper mount v1.0, Mini | | | Aleph Objects | | 1 | ea | $0.680 | $0.68
Printed | PP-GP0167 | Fan Mount v1.3, Mini | | | Aleph Objects | | 1 | ea | $1.170 | $1.17
Printed | PP-GP0190 | Lower relief v1.0 Mini | | | Aleph Objects | | 1 | ea | $0.190 | $0.19
Mechanical | HD-MS0211 | Borosilicate Glass Bed 170mm x 170mm | | | Allen Scientific | | 1 | ea | $6.750 | $6.75 | 1020
Hardware | HD-MS0027 | Spring, Extruder, 6mm OD, 0.8mm WD, 9.7mm FL | | | Associated Spring | C0240-032-0380-M | 2 | ea | $0.137 | $0.27 | 2100
Mechanical | HD-BL0015 | GT2, Single sided Neoprene Belt | B & B Manufacturing, Inc 744-2P-06 (2MR-744-06) | 2 | ea | $2.290 | $4.58 | 1020
Mechanical | HD-MS0033 | GT2 Timing Pulley, 5mm Bore Aluminum | B & B Manufacturing, Inc 16-2P06M6CA5 5MM BORE ALUMINUM2 | ea | $3.440 | $6.88 | 1020
Electronic | EL-PS0025 | POWER SUP 150W 24V 6.25A PNL MT | Delta | PMC-24V150W1AA DELTA | PMC-24V150W1AA | 1 | ea | $28.600 | $28.60 | 1020
Electronic | EL-MS0143 | Conn Fast Receptacle14-16 AWG .250 | | | TTI | 22-26AWG .110 | 7 | ea | $0.077 | $0.54 | 7100
Electronic | EL-MS0205 | CONN TERM MALE 22-24AWG TIN | Molex | | Digikey | WM2517TR-ND | 25 | ea | $0.038 | $0.96 | 2 reels
Electronic | EL-MS0212 | CONN PIN 24-30AWG CRIMP TIN | Molex | 16-02-0108 | Heilind | MOL16-02-0108 | 2 | ea | $0.056 | $0.11 | 2500
Electronic | EL-MS0059 | CONN TERM FEMALE 22-24AWG TIN | Molex Inc. | 16-02-0102 | Digikey | WM2510TR-ND | 73 | ea | $0.032 | $2.36 | 4 reels
Electronic | EL-MS0061 | Connector, 4 pin Male housing with latch | Molex | 701070003 | Digikey | WM2535-ND | 3 | ea | $0.140 | $0.42 | 4050
Electronic | EL-MS0062 | Connector, 4 pin Female housing with latch | Molex | 50579404 | Digikey | WM2902-ND | 8 | ea | $0.112 | $0.90 | 9100
Electronic | PC-CN0001 | CONN HOUSING 2POS .100 W/LATCH | | | TTI | WM2900-ND | 5 | ea | $0.062 | $0.31 | 6100
Electronic | PC-CN0003 | Connector Housing 3POS .100 W/Latch | | | TTI | WM2901-ND | 6 | ea | $0.060 | $0.36 | 6100
Electronic | EL-MS0142 | CONN RECEPT FASTON 22-26AWG .110 | | | TTI | A27793-ND | 12 | ea | $0.109 | $1.31 | 12100
Electronic | EL-MS0141 | Term Ring Non Ins 26-22AWG #4 | | P22-4R-M | Heilind | P22-4R-M | 6 | ea | $0.087 | $0.52 | 8200
Electronic | EL-MS0210 | CONN RING UNINS 15-20AWG #M3 | | | Digikey | A107160CT-ND | 2 | ea | $0.090 | $0.18 | 2050
Electronic | EL-SW0022 | SWITCH BASIC SPDT 3A .110QC 125V | | | Digikey | SW766-ND | 6 | ea | $0.520 | $3.12 | 6100
Electronic | EL-WR0099 | Shielded 4Cond 22AWG | | C0762A.41.10 | Digikey | W504-1000-ND | 2470 | mm | $0.001 | $3.02 | 9000 ft
Electronic | EL-WR0105 | 24AWG Stranded – Black | | C2015A.21.01 | Digikey | C2015B-1000-ND | 6025 | mm | $0.000 | $1.54 | 22000 ft
Electronic | EL-WR0107 | 24AWG Stranded – White | | C2015A.21.02 | Digikey | C2015W-1000-ND | 1100 | mm | $0.000 | $0.28 | 4000 ft
Electronic | EL-WR0109 | 24AWG Stranded – Yellow | | C2015A.21.05 | Digikey | C2015Y-1000-ND | 2090 | mm | $0.000 | $0.54 | 8000 ft
Electronic | EL-WR0103 | 24AWG Stranded – Red | | C2015A.21.03 | Digikey | C2015R-1000-ND | 3825 | mm | $0.000 | $0.98 | 14000 ft
Electronic | EL-WR0104 | 24AWG Stranded – Orange | | C2015A.21.04 | Digikey | C2015A-1000-ND | 2820 | mm | $0.000 | $0.72 | 11000 ft
Electronic | EL-WR0118 | 24AWG Stranded – Blue | | C2015A.21.07 | Digikey | C2015L-1000-ND | 460 | mm | $0.000 | $0.14 | 2000 ft
Electronic | EL-WR0119 | 24AWG Stranded – Green | | C2015A.21.06 | Digikey | C2015G-1000-ND | 520 | mm | $0.000 | $0.16 | 2000 ft
Electronic | EL-WR0120 | 24AWG Stranded – Purple | | C2015A.21.19 | Digikey | C2015V-1000-ND | 1210 | mm | $0.000 | $0.31 | 5000 ft
Electronic | EL-WR0106 | 16AWG Stranded – Red | | C2065A.21.03 | Digikey | C2065R-1000-ND | 400 | mm | $0.007 | $2.78 | 2000 ft
Electronic | EL-WR0121 | 16AWG Stranded – Black | | C2065A.21.01 | Digikey | C2065B-1000-ND | 1280 | mm | $0.007 | $8.89 | 4000 ft

V10R87-B08130

Electronic | EL-WR0122 | 16AWG Stranded – Green | | C2065A.21.06 | Digikey | C2065G-1000-ND | 125 | mm | $0.007 | $0.87 | 1000 ft
Electronic | EL-WR0123 | 16AWG Stranded – White | | C2065A.21.02 | Digikey | C2065W-1000-ND | 880 | mm | $0.007 | $6.11 | 2000 ft
Electronic | EL-WR0108 | 16AWG Stranded – Violet | | | Digikey | C2065V-1000-ND | 1100 | mm | $0.001 | $1.38 | 4000 ft
Electronic | EL-MS0216 | Ferrite Tubular Bead 19.00mm | Laird Techn | 28B1142-100 | Digikey | 240-2314-ND | 1 | ea | $0.335 | $0.34
Electronic | PC-CN0046 | Term Block Plug 4POS STR 5.08MM | | | Digikey | WM7953-ND | 1 | ea | $1.22 | $1.22 | 1050
Electronic | PC-CN0032 | Term Block Plug 2POS STR 5.08MM | | | TTI | WM7819-ND | 2 | ea | $0.46 | $0.91 | 2050
Electronic | EL-MS0074 | 20-POS .100 Dual (Black) | | | TTI | WM2527-ND | 2 | ea | $0.600 | $1.20 | 2040
Electronic | EL-MS0211 | REEL – RING TONGUE CONN 16-22 AWG #10 PIDG | TE | 2-36154-2 | Digikey | A1062TR-ND | 7 | ea | $0.120 | $0.84 | 7000
Hardware | HE-SH0031 | Reprap Modified Hexagon Hotend, Lulzbot Edition, 3.0mm Filament | Reprapdiscount | 1 | ea | $23.000 | $23.00 | 1020
Mechanical | PP-FP0055 | Left Plate, | | | EPOCS | | 1 | ea | 19.500 | $19.50 | 200
Mechanical | PP-FP0052 | Right Plate, | | | EPOCS | | 1 | ea | 12.750 | $12.75 | 200
Mechanical | PP-FP0051 | Top Plate, | | | EPOCS | | 1 | ea | 21.000 | $21.00 | 200
Mechanical | PP-FP0053 | Bottom Plate, | | | EPOCS | | 1 | ea | 32.250 | $32.25 | 200
Mechanical | PP-FP0054 | Bed Mount Plate, | | | EPOCS | | 1 | ea | 8.250 | $8.25 | 200
Mechanical | PP-FP0056 | Electronics cover, | | | EPOCS | | 1 | ea | 19.000 | $19.00 | 200
Mechanical | PP-FP0055 | Left Plate, | | | Rapid Sheet Metal | | 1 | ea | 19.500 | | 810
Mechanical | PP-FP0052 | Right Plate, | | | Rapid Sheet Metal | | 1 | ea | 12.750 | | 810
Mechanical | PP-FP0051 | Top Plate, | | | Rapid Sheet Metal | | 1 | ea | 21.000 | | 810
Mechanical | PP-FP0053 | Bottom Plate, | | | Rapid Sheet Metal | | 1 | ea | 27.750 | | 810
Mechanical | PP-FP0054 | Bed Mount Plate, | | | Rapid Sheet Metal | | 1 | ea | 8.250 | | 810
Mechanical | PP-FP0056 | Electronics cover, | | | Rapid Sheet Metal | | 1 | ea | $19.00 | | 810
Hardware | EL-MS0165 | Snap-Together Cable and Hose Carrier, Feed-Through, 0.41" High x 0.39" Wide Interior SiIGUS | 06-10-028-0 | 813 | mm | $0.020 | $16.47 | 2800 feet
Hardware | EL-MS0166 | Mounting Brackets for .41" High x .39" Wide Interior Snap-Together Cable and Hose CarrIGUS | 060-10-12 | 3 | ea | $3.330 | $9.99 | 3030
Mechanical | HD-BU0013 | DryLin® R - Solid polymer bearing RJM-01, 8mm | | | IGUS | RJM-01-08 | 12 | ea | $2.00 | $24.00 | 12100
Electronic | EL-FA0011 | FAN,24VDC,Sleeve,5.75CFM,40X40X10MM,60mA 6000RPM,1.44W,2 TF4010-24H-S | Kysan | 69829 | 1 | ea | $1.550 | $1.55 | 1050
Electronic | EL-FA0012 | FAN,24VDC,BALL,31.60CFM,80×80×15 MM,100mA | | TF8015-24M-B | Kysan | 69866 | 1 | ea | $2.55 | $2.55 | 1010
Mechanical | HD-RD0035 | 8mm Smooth rod, 315mm, 304 Stainless Steel | | | MBK | | 6 | ea | $8.900 | $53.40 | 6060
Mechanical | HD-RD0004 | 8mm Smooth Rod x 18-19mm | | | MBK | | 1 | ea | $4.60 | $4.60 | 1010
Hardware | HD-BT0108 | Hobbed Bolt, M8 x 50mm Hex head, 26mm offset, Stainless Steel | Quattro | 1 | ea | $5.870 | $5.87 | 1010
Hardware | PP-MP0082 | Bed leveling washer, 303 SST | | | MBK | | 4 | ea | $2.900 | $11.60 | 4040
Electronic | TL-CS0083 | EMI/RFI-Shield Heat-Shrink Tubing 3/16" ID Before, 3/32" ID ATechflex | H2C0.19BK | Allcable | H2C0.19BK | 450 | mm | $0.01 | $5.96 | 285x 4 ft pieces
Electronic | TL-CS0129 | Interference-Shielding Heat-Shrink Tubing, 3/8" ID Before, 3/1Techflex | H2C0-38BK | Allcable | H2C0-38BK | 125 | mm | $0.02 | $2.97 | 103x 4 ft pieces
Hardware | HD-WA0035 | Metric 18-8 Stainless Steel External Serrated Lock Washer, M3 Screw Size, 6mm OD, 0.4mm mMcmaster | 91120A120 | 4 | ea | $0.020 | $0.08 | 4100
Hardware/tools | HD-MS0244 | Firm White Polyester Felt Strip, 1/4" Thick, 1" Width, Plain Back | Mcmaster | 88085K311 | 270 | mm | $0.001 | $0.38 | 900 ft
Hardware | HD-MS0235 | Metric Aluminum Unthreaded Spacer, 4.5mm OD, 8mm Length, M3 Screw Size | Mcmaster | 94669A615 | 4 | ea | $0.350 | $1.40 | 4050
Electronic | EL-MS0073 | Tubing, Corrugated Loom .25" | Panduit | 708161 | Fastenal | 708161 | 695 | mm | $0.000 | $0.20 | 24x 100ft rolls
Hardware | HD-BT0117 | Black Alloy Steel Flat-Head Socket Cap Screw, Class 10.9, M8 Size, 40mm Length, 1.25mm PiTimberline | 1 | ea | $0.12 | $0.12 | 1020
Hardware | HD-BT0131 | Black Alloy Steel Flat-Head Socket Cap Screw, Class 10.9, M8 Size, 45mm Length, 1.25mm PiTimberline | 1 | ea | $0.13 | $0.13 | 1020
Hardware | PP-MP0066 | Metric Brass Heat-Set Insert for Plastics, Tapered, M2-.4 Internal Thread, 2.9MM Length | Mcmaster | 94180A307 | 13 | ea | $0.10 | $1.34 | 13000
Hardware | HD-BT0107 | Metric Class 12.9 Socket Head Cap Screw Alloy Steel, Black, M2 Thread, 10mm Length, 0.4mmFastenal | 12 | ea | $0.02 | $0.26 | 12000
Hardware | HD-WA0012 | Steel Flat Washer, DIN 125 zinc-plated class 4,M2 screw sz, 5mm OD, | 40350 | Fastenal | 40350 | 12 | ea | $0.00 | $0.02 | 12000
Hardware | HD-MS0230 | M2 x 6 SHCS, Black-Oxide | | | Timberline | | 1 | ea | $0.04 | $0.04 | 1050
Hardware | HD-MS0030 | M3-.5 3.8mm Heatset Insert | | 11125995 | Fastenal | 11125995 | 79 | ea | $0.06 | $4.70 | 79000
Hardware | HD-MS0158 | M5-.8 6.7mm Heatset Insert | | 11125997 | Fastenal | 11125997 | 13 | ea | $0.15 | $1.94 | 13000
Hardware | HD-NT0001 | M3 Nyloc Nut, Zinc Plated | | | Timberline | | 6 | ea | $0.01 | $0.07 | 6100
Hardware | HD-NT0004 | M3 Nut, Zinc Plated | | | Timberline | | 3 | ea | $0.01 | $0.03 | 3000
Hardware | HD-BT0012 | M3 Set Screw (Grub Screw) | NS0310-0306/met Mcmaster | 91390A100 | 7 | ea | $0.02 | $0.13 | 7000
Hardware | HD-WA0001 | M3 Washer, Steel, Zinc Plated | | | Timberline | MTR-M3100321 | 61 | ea | $0.00 | $0.10 | 61000
Hardware | HD-BT0044 | M3 x 5 Bolt, SHCS Black-Oxide | 39501 | 39501 | Fastenal | 39501 | 4 | ea | $0.02 | $0.09 | 4000
Hardware | HD-BT0128 | M3 x 6 Bolt, FHCS Black-Oxide | | | mcmaster | 91294A126 | 97 | ea | $0.040 | $3.88 | 98000
Hardware | HD-BT0104 | M3 x 8 Bolt, BHCS, SST | | | mcmaster | 92095A181 | 3 | ea | $0.094 | $0.28 | 3030
Hardware | HD-BT0137 | M3 x 8 Bolt, BHCS, Black-Oxide | | | Timberline | | 17 | ea | $0.065 | $1.10 | 18000
Hardware | HD-BT0039 | M3 x 12 Bolt, SHCS Black-Oxide | | | Timberline | 8050-0312 | 45 | ea | $0.01 | $0.53 | 45000
Hardware | HD-BT0118 | M3 x 14 Bolt FHCS, Black-Oxide | | | mcmaster | 91294A133 | 2 | ea | $0.061 | $0.12 | 2050
Hardware | HD-BT0136 | M3 x 12 Bolt FHCS, SST | | | Timberline | | 4 | ea | $0.060 | $0.24 | 4100
Hardware | HD-BT0135 | M3 x 25 Bolt FHCS, Black-Oxide | | | mcmaster | 91294A138 | 4 | ea | $0.08 | $0.32 | 4100
Hardware | HD-BT0041 | M3 x 25 Bolt, SHCS Black-Oxide | | | Timberline | 8050-0325 | 1 | ea | $0.03 | $0.03 | 1000
Hardware | HD-NT0011 | M4 Nut,Zinc-Plated Steel | | | Timberline | 8100-0040 | 4 | ea | $0.01 | $0.02 | 4000

Hardware | HD-WA0005 | M4 Washer | Timberline | 8200-0040 | 6 | ea | $0.00 | $0.02 | 6000
Hardware | HD-MS0229 | M4 x 25 Bolt, SHCS Black-Oxide | mcmaster | 91290A176 | 2 | ea | $0.137 | $0.27 | 2020
Hardware | HD-BT0052 | M4 x 55 Bolt, SHCS Black-Oxide | Timberline | NS8050-0455 | 2 | ea | $0.08 | $0.16 | 2000
Hardware | HD-WA0007 | M5 Washer, Steel, Zinc Plated | mcmaster | 91166A240 | 11 | ea | $0.022 | $0.24 | 11200
Hardware | HD-BT0048 | M5 x 10 Bolt, SHCS Black-Oxide | Timberline | 8050-0510 | 6 | ea | $0.02 | $0.13 | 6000
Hardware | HD-BT0049 | M5 x 14 Bolt, SHCS Black_Oxide | Timberline | NOR-M60051014SO | 5 | ea | $0.03 | $0.13 | 5000
Hardware | HD-NT0002 | M8 Nyloc Nut, Zinc Plated | Timberline | GBO-986270004 | 3 | ea | $0.05 | $0.16 | 3000
Hardware | HD-WA0006 | M8 Washer, Steel, Zinc Plated | Timberline | 8200-0080 | 9 | ea | $0.01 | $0.11 | 9100
Hardware | HD-WA0008 | Metric Spring Steel Shim - DIN 988 0.5mm Thick, 8mm ID, 14mm OD | Timberline | 1 | ea | $0.05 | $0.05 | 1000
Hardware | HD-WA0009 | Metric Spring Steel Shim - DIN 988 1.0mm Thick, 8mm ID, 14mm OD | Timberline | 1 | ea | $0.06 | $0.06 | 1000
Hardware | HD-MS0031 | Thumb Screw Knob for M4 SHCS, Black | Timberline | 2 | ea | $0.10 | $0.19 | 2000
Hardware | HD-BT0120 | 92981A100 | Mcmaster | 7130k32 | 2 | ea | $1.030 | $2.06 | 2020
Hardware | HD-MS0058 | Wire Tie, 8" | Timberline | AEH#02-00818-UVB | 12 | ea | $0.02 | $0.28 | 12000
Hardware | HD-MS0249 | UV-Resistant Cable Tie Holder, Adhesive Back/Screw Mount, 4-Way, for.18" Maximum Tie, Bla Mcmaster | 7582k22 | 2 | ea | $0.249 | $0.50 | 2050
Consumable | TL-CS0040 | Extreme-Temperature Pipe Sealant & Threadlocker, 4 oz bottle, blue | Mcmaster | 7604A55 | 0.5 | g | $0.066 | $0.03 | 5 bottles
Mechanical | HD-RD0036 | Drive Rod 10mm | Thomson | 2 | ea | $28.100 | $56.20 | 2020
Mechanical | HD-NT0047 | 10mm x 2mm Flange mount supernut | MTS10 x 2m | Thomson | 2 | ea | $6.780 | $13.56 | 2020
Mechanical | HD-MS0194 | Coupling, Set Screw, Misumi GSASL16-5-5 | Misumi | GSASL16-5-5 | 2 | ea | $7.50 | $15.00 | 2050
Mechanical | HD-MS0255 | Ultem PEI, 0.010" x 12" x 90ft rolls | Professional Plastics | 160 | mm | $0.034 | $5.51 | 10 rolls
Mechanical | HD-MS0254 | S-13994 3M 468MP Adhesive Transfer Tape - 12" x 60 yards | Uline | S-13994 | 160 | mm | $0.005 | $0.78 | 5 rols
Electronic | EL-CA0030 | 6ft 18AWG Power Cord Cable w/ 3 Conductor PC Power Connector Socket (C13/5-15P) – Bla Monoprice | 5279 | 1 | ea | $1.65 | $1.65 | 1010
Electronic | EL-CA0001 | 6ft USB 2.0 A Male to B Male 28/24AWG Cable | 3021007-06 | Heilind | QTK3021007-06 | 1 | ea | $1.05 | $1.05 | 1010
Electronic | PP-MP0028 | AC Power Entry Modules SC MT FUSED .25" TAB | Mouser | 161-PF0030/63 | 1 | ea | $3.16 | $3.16 | 1010
Electronic | EL-MS0096 | Cartridge Fuses 125V 7A 5X20 MA UL LBC | Mouser | 576-0233007.MXP | 2 | ea | $0.45 | $0.89 | 2050
Electronic | EL-WR0040 | Wire - Single Conductor 20AWG SOLID PTFE, RED | Mouser | 602-2856/1-100-03 | 185 | mm | $0.00 | $0.72 | 8 rolls
Electronic | EL-MS0008 | Heavy Duty Power Connectors HOUSING ONLY, BLACK POWERPOLE 15/45 | Mouser | 879-1327G6-BK | 2 | ea | $0.16 | $0.32 | 2050
Electronic | EL-MS0010 | Heavy Duty Power Connectors POWERPOLE 15A CONT | Mouser | 879-1332-BK | 2 | ea | $0.10 | $0.20 | 2050
Electronics | PC-BD0029 | Silicon Heater, 24V, 168mm x 168mm, Self Adhesive, w/ connectors | National Plastic Heater | 1 | ea | $27.95 | $27.95 | On Order
Electronic | EL-FA0020 | RFB2008 Micro Blower | Pelonis | 1 | ea | $6.68 | $6.68 | 1050
Electronic | EL-SW0023 | SWITCH ROCKER DPST 20A 250V, illuminated red | E-Switch | R5BBLKREDFF2 Digikey | EG1535-ND | 1 | ea | $1.702 | $1.70 | 1100
Electronic | EL-MT0001 | NEMA 17 Stepper Motors | Changzhou FTX Motors Co.,SY42STH47-1504A | 5 | ea | $7.50 | $37.50 | On Order
Electronic | PC-BD0049 | Mini RAMBo, assembled board only with no LCD headers | UltiMachine | 1 | ea | $57.00 | $57.00 | 1020
Mechanical | HD-MS0204 | Sealed Skateboard/inline/Rollerblade Skate Bearing Ball Bearings | vxb.com | Kit708 | 11 | ea | $0.20 | $2.20 | 11000
Etching | PP-FP0058 | Laser Engraving Designs | 1 | ea | $9.91 | $9.91 | 810
Packaging | SH-PG0075 | 1.5# RECY & 2# CROSSLINK W/ 10030 CH URETHANE | Shipper's Supply | 20140922SA | 1 | ea | $20.53 | $20.53 | 1010
Packaging | SH-PG0076 | 22x17x19 275# dw white/ OUTSIDE PRINT 2 COLOR | Shipper's Supply | 1 | ea | $3.70 | $3.70 | 1010
Packaging | SH-PG0085 | 3" x 55 yards 3.1 Mil Uline Clear Carton Sealing Tape 24 rolls/case | 0.018 | pc | $4.95 | $0.09
Packaging | DC-LB0028 | Label, Lulzbot Mini Barcode | 1 | ea | $0.14 | $0.14
Packaging | DC-LB0029 | Mini v1 serial number sticker | 1 | ea | $0.01 | $0.01
Packaging | RM-HI0024 | HIPS, 1 meter Sample, Random Color | 1 | ea | $0.03 | $0.03
Packaging | SH-PG0002 | 3 x 4" 2 Mil Reclosable Polypropylene Bags | 1 | ea | $0.02 | $0.02
Packaging | SH-PG0083 | 9 x 12" 8 Mil Reclosable Bags | 1 | ea | $0.29 | $0.29
Packaging | SH-PG0084 | 6 x 10" 6 Mil Reclosable Bags | 1 | ea | $0.18 | $0.18
Packaging | DC-MS0028 | Packing List, Mini 1.0 | 1 | ea | $0.24 | $0.24
Packaging | DC-MS0029 | Quality assurance record Mini 1.0 | 1 | ea | $0.72 | $0.72
Tools | TL-MS0020 | .003 Stainless Steel/Straight Instrument Cleaner Brush | GORDON BRUSH MFG CO, | 906501 | 1 | ea | $5.29 | $5.29 | 1020
Tools | EL-MS0220 | SWM Style USB Flash drive, 4gb, black | USB Memory Direct | 1 | ea | $4.15 | $4.15 | 1020
Tools | TL-HD0046 | Pro Dental Pick, 5 3/4 in | Image Supply | (DP-19) M S V | 1 | ea | $1.87 | $1.87 | 1010
Tools | TL-HD0009 | 7 1/2" Nylon Handle Clam Knife | WEBstaurant Store | 35340592 | 1 | ea | $2.030 | $2.03
$752.61
Total Lulz | 1,000 | Needs something
Good to Order
Ordered

Alloy Steel Shoulder Screw, 6mm Diameter x 10mm Long Shoulder, M5 Thread

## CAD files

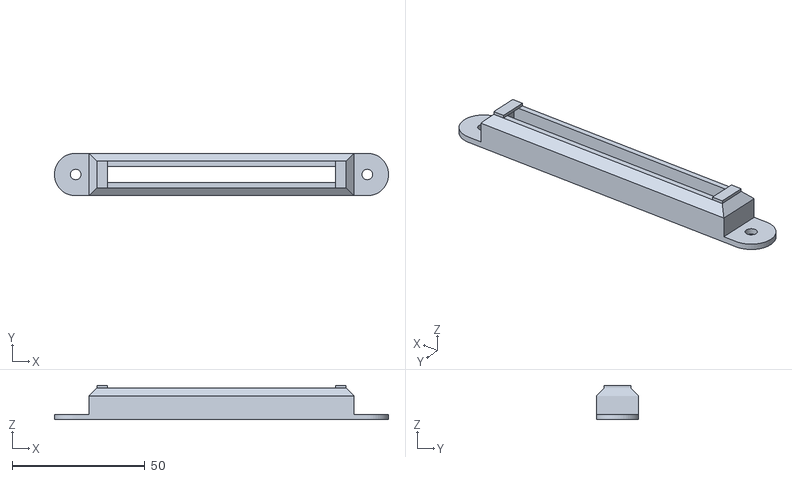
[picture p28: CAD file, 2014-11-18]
STL/wipermount.stl
126.0 x 16.0 x 13.0

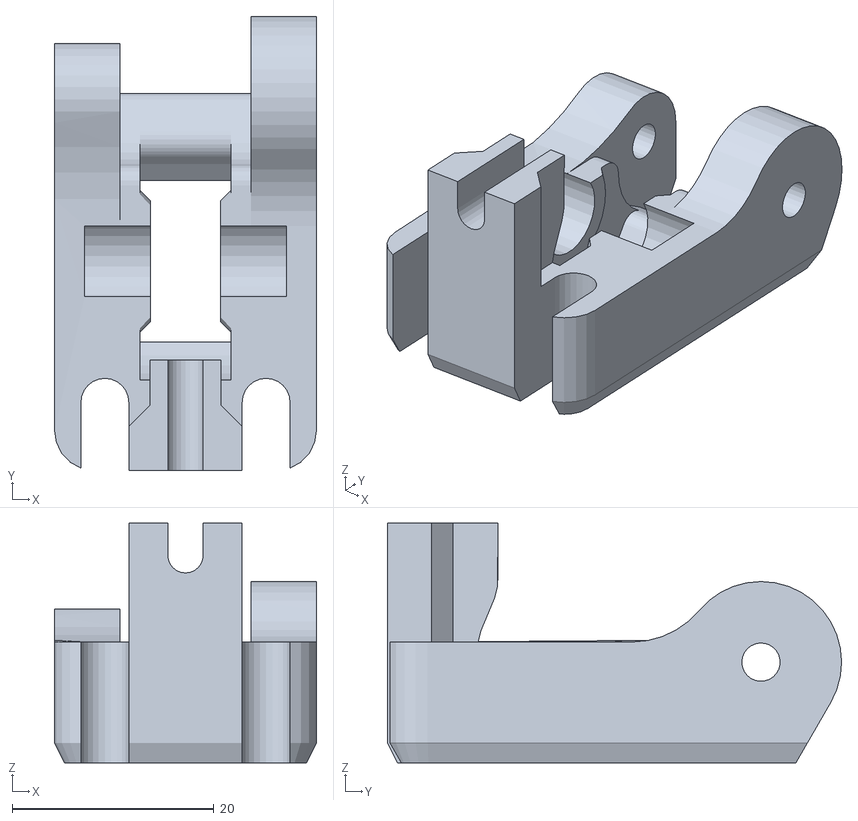
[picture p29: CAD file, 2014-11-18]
STL/idler.stl
26.0 x 45.1 x 23.8

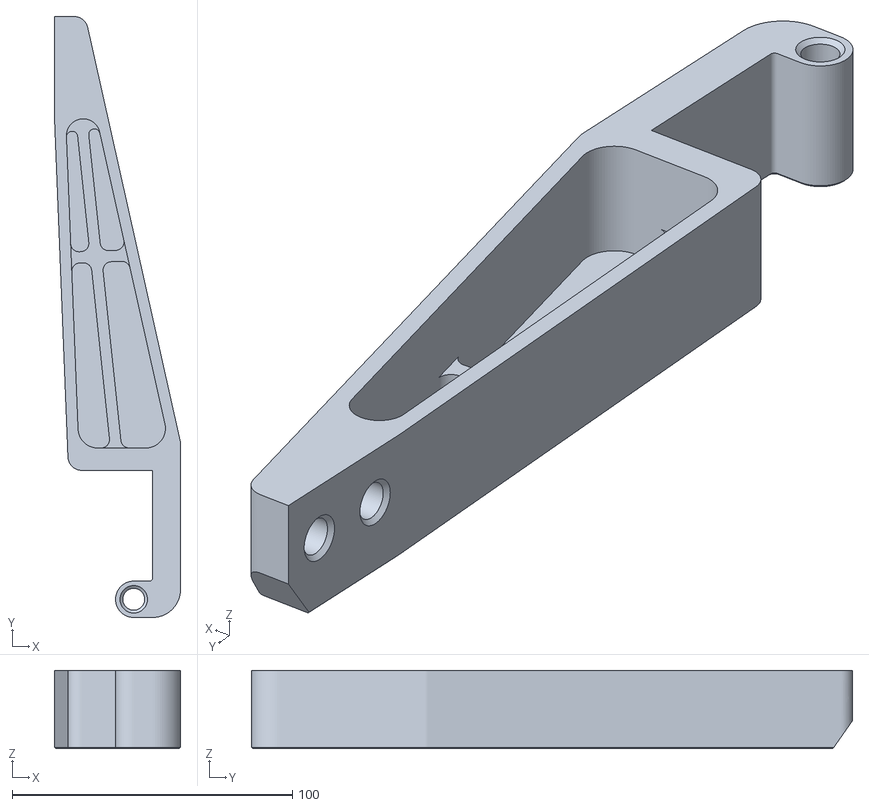
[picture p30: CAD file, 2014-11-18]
STL/spoolmount.stl
45.0 x 214.5 x 28.0

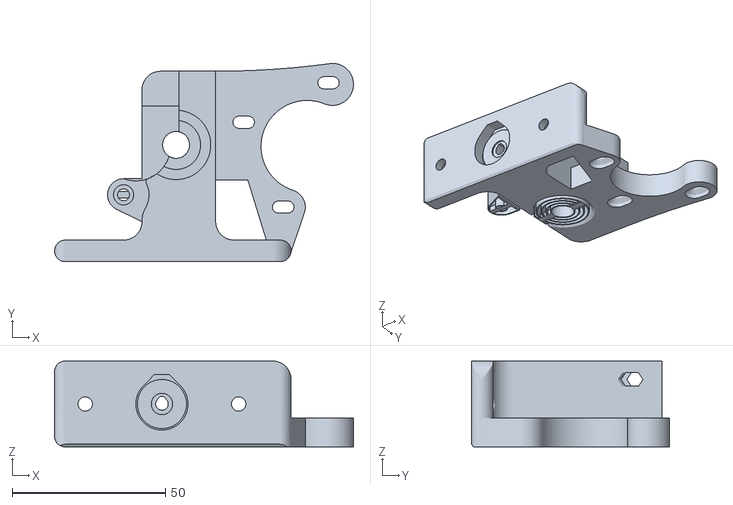
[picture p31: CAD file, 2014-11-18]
STL/extruderbody.stl
97.4 x 64.5 x 28.0

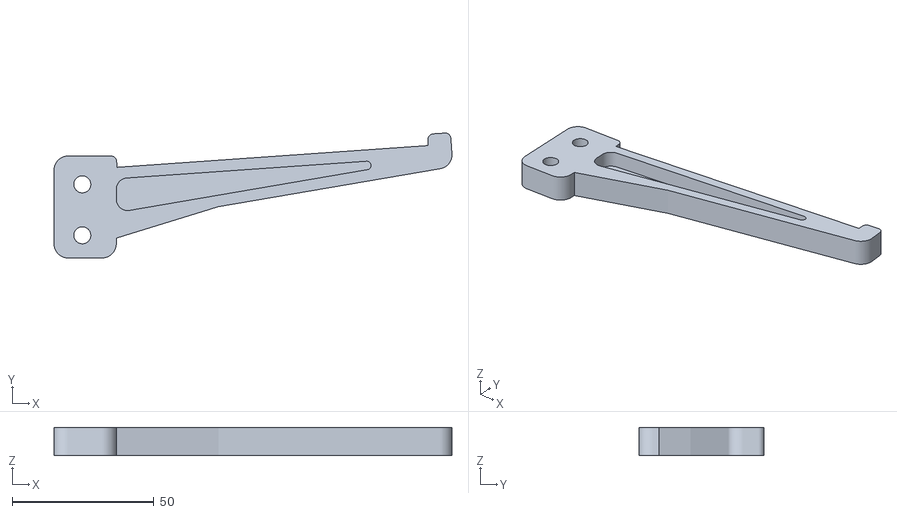
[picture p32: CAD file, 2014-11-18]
STL/spoolarm.stl
140.5 x 44.1 x 10.0

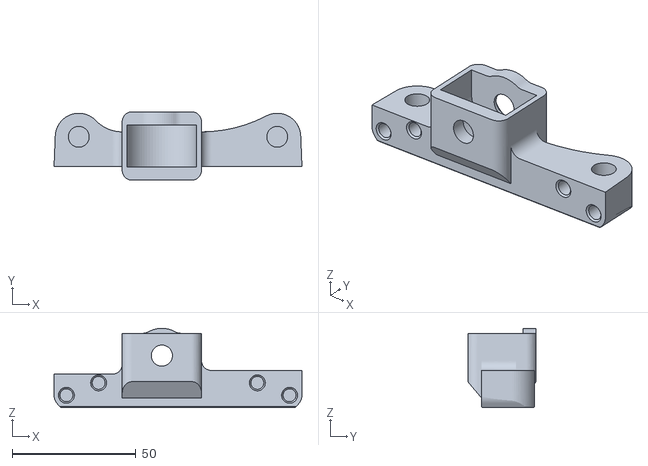
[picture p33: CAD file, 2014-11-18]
STL/yendidler.stl
100.0 x 27.6 x 32.0

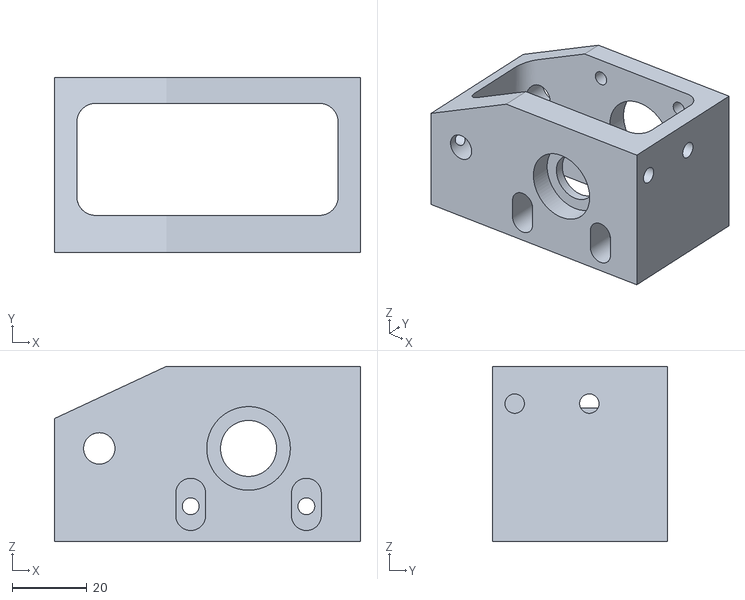
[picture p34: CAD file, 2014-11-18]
STL/lowzright.stl
82.0 x 47.0 x 47.0

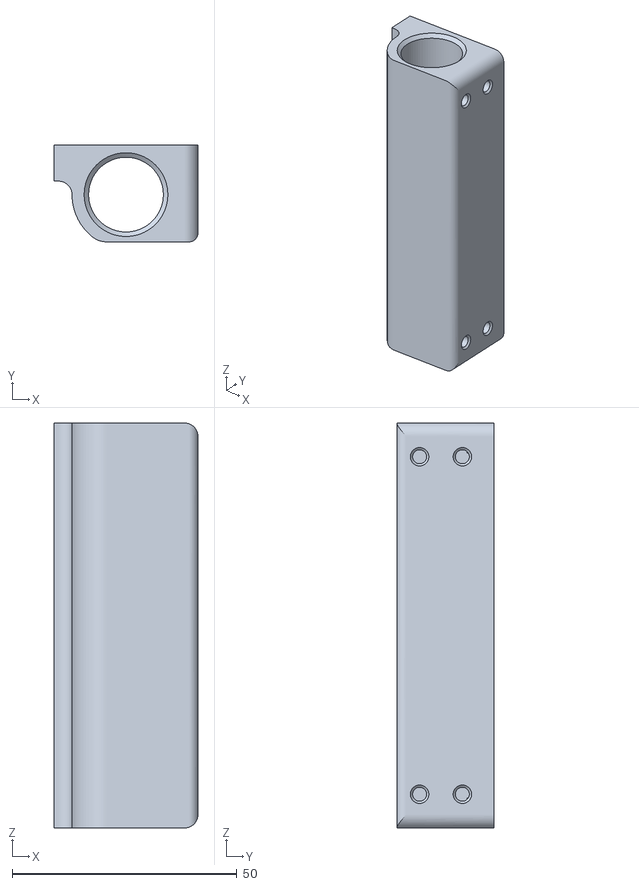
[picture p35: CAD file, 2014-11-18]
STL/doublebearingholder.stl
32.0 x 21.5 x 90.0

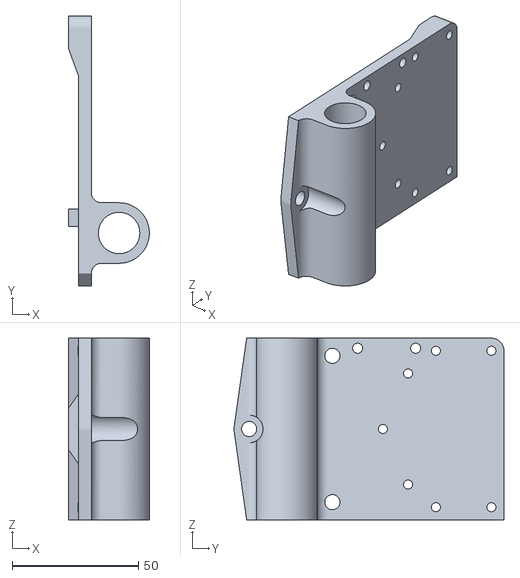
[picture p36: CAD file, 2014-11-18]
STL/xcarriage.stl
32.0 x 107.0 x 72.0

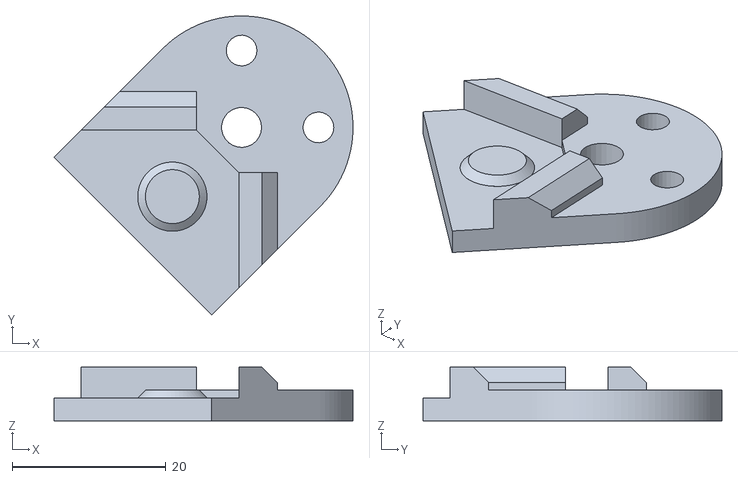
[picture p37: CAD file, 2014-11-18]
STL/bedcorner.stl
38.9 x 38.9 x 7.00

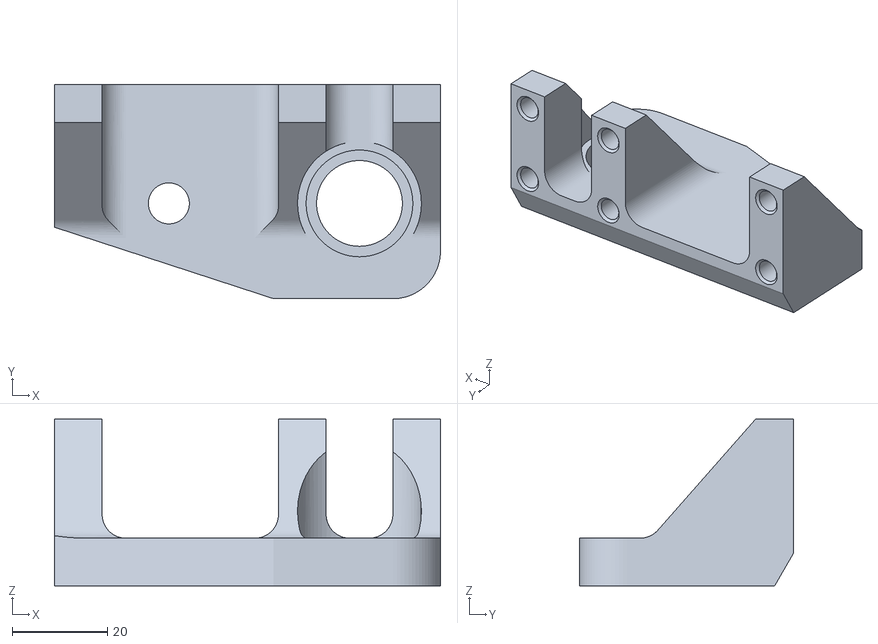
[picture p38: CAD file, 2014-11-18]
STL/upzright.stl
81.0 x 45.0 x 35.0

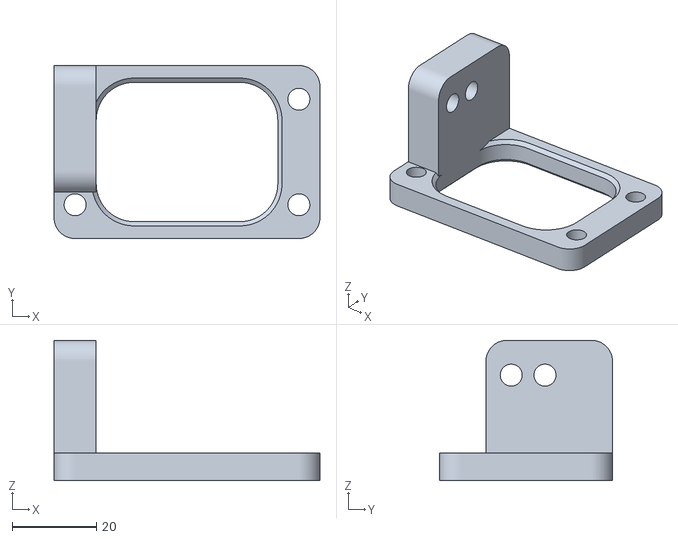
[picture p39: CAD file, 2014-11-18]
STL/reliefmount.stl
63.0 x 41.0 x 33.2

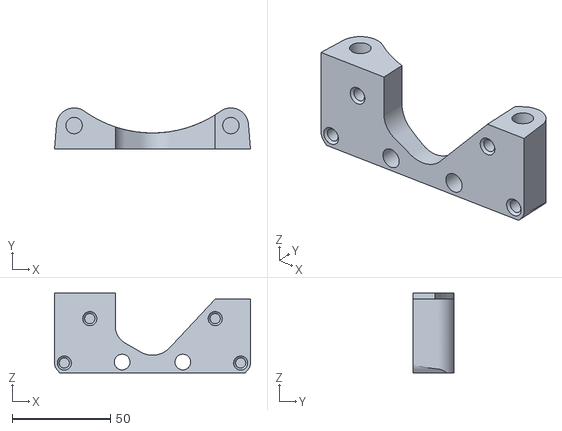
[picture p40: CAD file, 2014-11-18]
STL/yendrodmount.stl
100.0 x 21.0 x 40.6

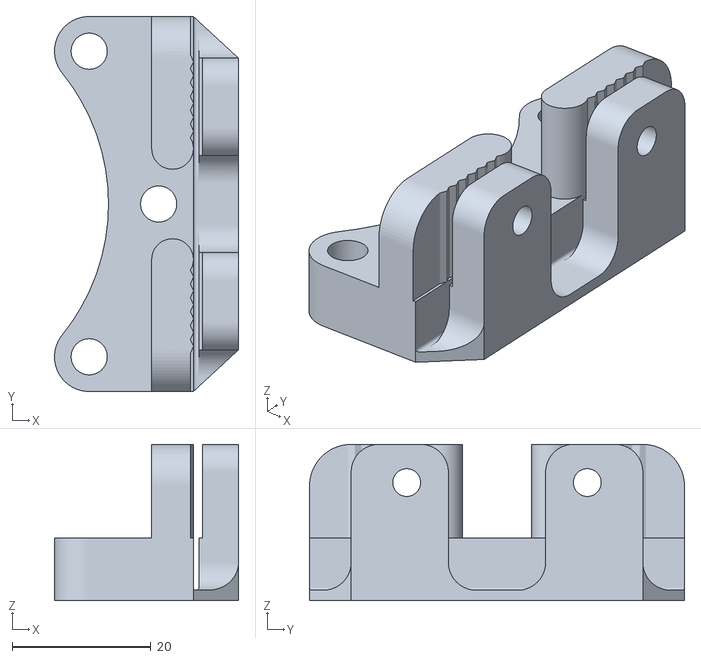
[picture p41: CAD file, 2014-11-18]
STL/beltmount.stl
26.5 x 54.0 x 22.5

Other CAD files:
STL/upzleft.stl
STL/lowrelief.stl
STL/spoolhinge.stl
STL/lowzleft.stl
STL/extruderlatch.stl
STL/extrudermount.stl
STL/fanmount.stl
STL/gearlarge.stl
STL/gearsmall.stl
STL/handlebar.stl
STL/upperbearingholder.stl
STL/xcarriagecover.stl
STL/xendidler.stl
STL/xendmotor.stl

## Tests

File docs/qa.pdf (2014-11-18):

## QUALITY ASSURANCE RECORD

Page 1 of 3

### Model: LulzBot Mini 1.0 3D Printer

Serial Number: | ______________________
Date Completed: | ______________________
Tested by: | ______________________

Configuration:

Electronics: | Mini-RAMBo 1.0a
Firmware: | Marlin for Mini 2014-Q4
Nozzle: | 0.5mm diameter nozzle
Settings:
Stepper Motor | Steps/mm | Max Length | Microstep Mode | Digipot
X | 100.5 | 155 | 16 | 175
Y | 100.5 | 155 | 16 | 175
Z | 1600 | 155 | 16 | 220
E0 | 833 | NA | 16 | 135

General:

θ Are all the screws and zip ties tight?
θ Are the current version of parts being used?
θ Is the Spool Mount properly mounted so it flips up and sits securely? θ Is the Finger Clip properly mounted with the taller side on the left? θ Are the switches tight? They shouldn't wiggle side to side.
θ Are all 4 rubber feet installed?
θ Is the PEI tape free of bubbles and wrinkles?
θ Is the heat bed adhesive smooth and consistent with no finger prints?

Y Axis:

θ Does the Y bed move freely back and forth?
θ Is the belt mounted in the correct orientation?
θ Is the Y bed tight side to side from motion and twisting?
θ Are all the screws on the bearing holders tight?
θ Does the Y belt rub the bottom of the y-idler by the bearings?
θ Is the Y pulley tight?
θ Is one of the set screws on the Y pulley aligned with the flat on the motor shaft?
θ Are both pulley set screws tightened?
θ Is the level of the Y pulley at the same height as where the belt mounts on the belt holder? θ Is the Y belt tight?
θ Are the four bed leveling washers tight?
θ Are the belts trimmed far enough to not interfere with the pulley or bearing?

## QUALITY ASSURANCE RECORD

Page 2 of 3
X Axis:

θ Is the X pulley tight?
θ Is one of the set screws on the X pulley aligned with the flat on the motor shaft? θ Are both pulley set screws tightened?
θ Is the belt mounted in the correct orientation?
θ Is the belt free from rubbing anywhere during motion?
θ Is the X belt tight?
θ Does the X axis move freely end to end?
θ Are the X bars flush with the right side?
θ Are the set screws that hold the X bars tight?
θ Are the belts trimmed far enough to not interfere with the pulley or bearing?

Z Axis:

θ Do the Z drive rods rotate smoothly with no up and down movement between the bearings? θ Are the set screws that hold the Z bars tight?
θ Are the coupler set screws tight?
θ Are the drive rods and motor shafts aligned so the couplers are not bent?

Extruder:

θ Can you adjust the extruder springs?
θ Are the V grooves on the extruder gears lined up? θ Is the extruder mount secure on the X carriage? θ Is the extrusion fan mounted correctly?
θ Is the extruder blower mounted correctly?
θ Does the idler bearing stick out of the idler block?
θ Is the hobbing aligned to the hole in the extruder?
θ Is the set screw in the small gear tight and on the flat of the motor shaft? θ Can you feed filament about 100mm from the top of the extruder?
θ Are the gears tight with no back-lash?
θ Do the extruder gears turn smoothly for several rotations?

Electronics:

θ Are all connections to the Mini-Rambo plugged in correctly? θ Can you plug in USB cable from the outside of the enclosure? θ Is the case fan plugged in?
θ Are all cables free from contacting any moving parts?

## QUALITY ASSURANCE RECORD

Page 3 of 3
Test and Verification Results:

θ Verify case fan is running.
θ Verify extruder blower is running.
θ Verify control of the extrusion fan.
θ Nozzle temperature control verified.
θ Nozzle re-tightened during first heat cycle.
θ Extruder control verified.
θ X, Y, and Z min and max stop switches verified.
θ X and Y homing are making contact with bed leveling washer. θ Bed leveling is functioning properly.
θ Bed temperature control verified.
θ Bearing conditioning complete.
θ X, Y, and Z motion smooth over full range and speeds. θ Test print (Rocktopus*) successful.
θ Print head moved to shipping position.

*Rocktopus by Kent Johnson is licensed under CC BY-SA 4.0 and derived from work by dietz1 and yeoldebrian - lulzbot.com/rocktopus

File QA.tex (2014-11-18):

%
% QA.tex
% QA Development
%
% LulzBot Mini Developer's Guide
%
% Copyright (C) 2014 Aleph Objects, Inc.
%
% This document is licensed under the Creative Commons Attribution 4.0
% International Public License (CC BY-SA 4.0) by Aleph Objects, Inc.
%

\section{Quality Assurance}

\includepdf[addtolist={1,figure,{Quality Assurance},qadoc},pages=-,landscape=false,reflect=false,turn=false,fitpaper=true,keepaspectratio=true]{qa.pdf}

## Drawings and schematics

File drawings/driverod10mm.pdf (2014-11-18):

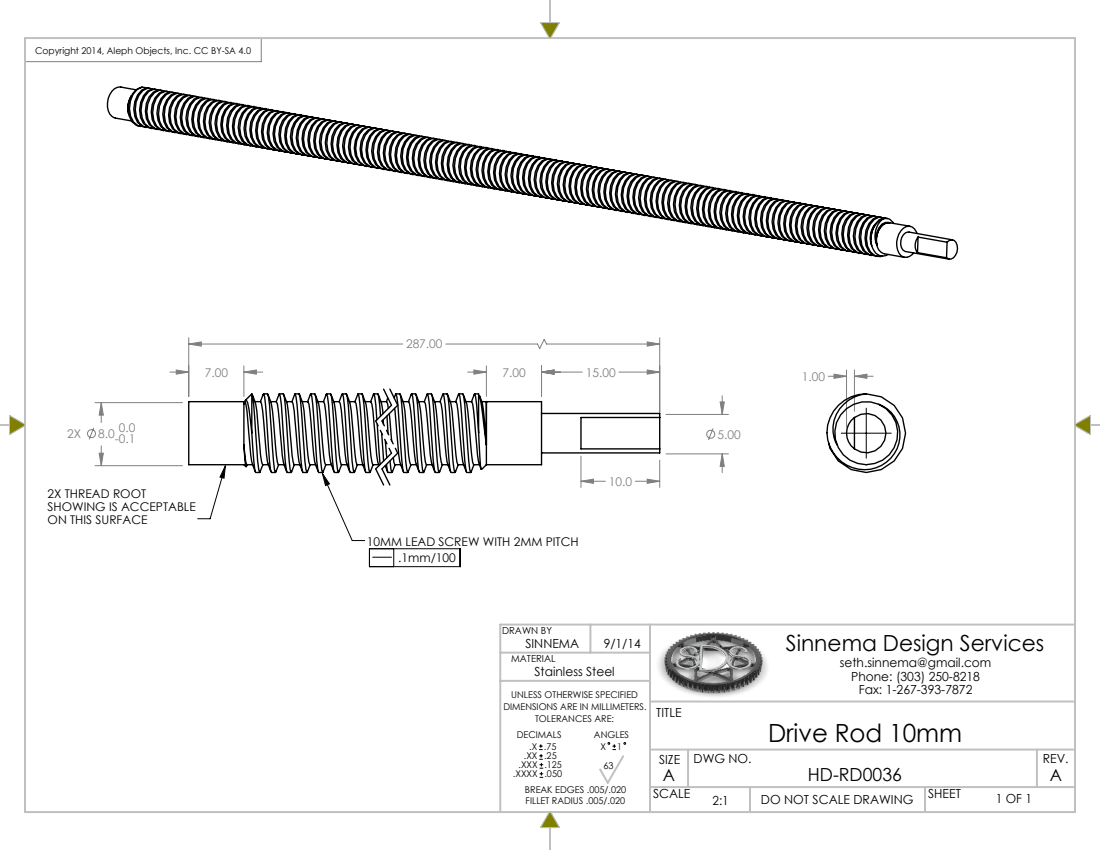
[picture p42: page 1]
Stainless Steel; DRAWN BY; SCALE; 1 OF 1 SHEET; DWG NO.; REV.

Copyright 2014, Aleph Objects, Inc. CC BY-SA 4.0

2X THREAD ROOT
SHOWING IS ACCEPTABLE
ON THIS SURFACE

10MM LEAD SCREW WITH 2MM PITCH

Sinnema Design Services

seth.sinnema@gmail.com
Phone: (303) 250-8218
Fax: 1-267-393-7872
Drive Rod 10mm
DO NOT SCALE DRAWING

UNLESS OTHERWISE SPECIFIED
DIMENSIONS ARE IN MILLIMETERS.
TOLERANCES ARE:
DECIMALS
.XXX .125
.XXXX .050
BREAK EDGES .005/.020
FILLET RADIUS .005/.020

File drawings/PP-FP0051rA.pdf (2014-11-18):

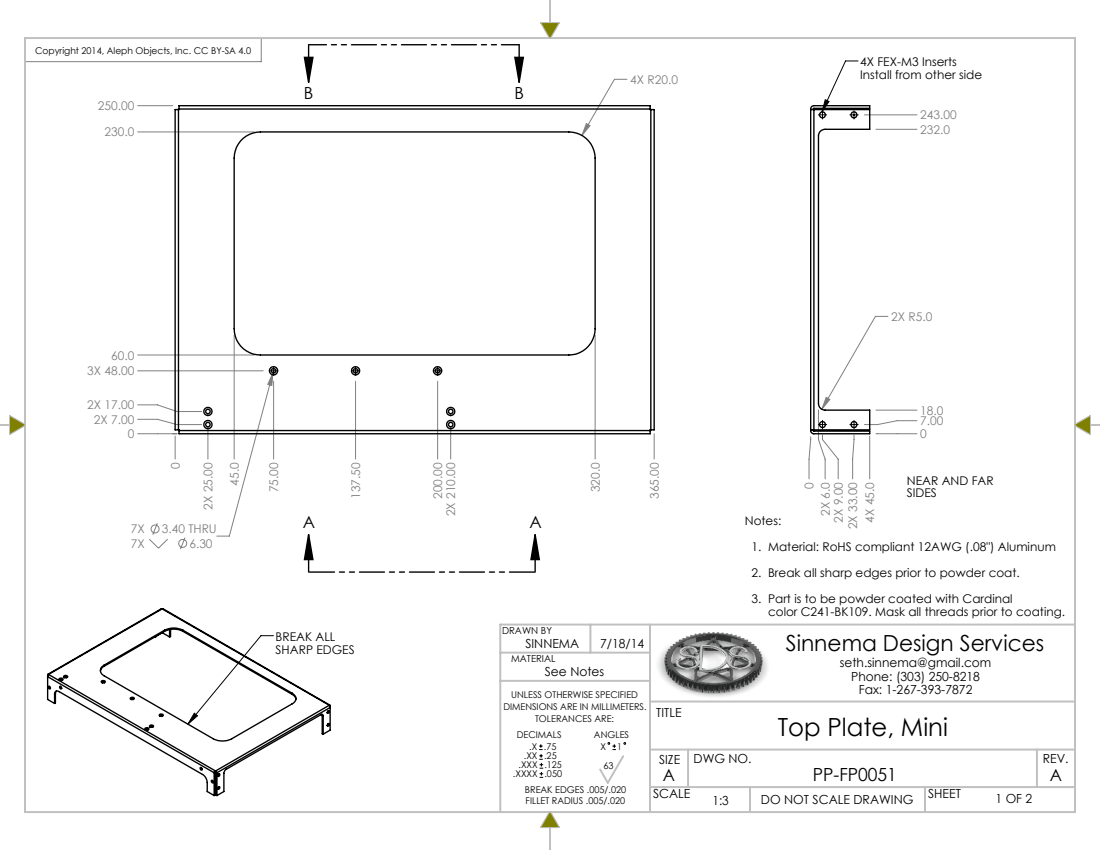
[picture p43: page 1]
BREAK ALL SHARP EDGES; 7X 3.40 THRU; See Notes; DRAWN BY; SCALE; 1 OF 2 SHEET; DWG NO.; REV.

Copyright 2014, Aleph Objects, Inc. CC BY-SA 4.0

4X FEX-M3 Inserts
Install from other side

NEAR AND FAR
SIDES

Notes:
1. Material: RoHS compliant 12AWG (.08") Aluminum
2. Break all sharp edges prior to powder coat.
3. Part is to be powder coated with Cardinal
color C241-BK109. Mask all threads prior to coating.
Sinnema Design Services

seth.sinnema@gmail.com
Phone: (303) 250-8218
Fax: 1-267-393-7872

UNLESS OTHERWISE SPECIFIED
DIMENSIONS ARE IN MILLIMETERS.
TOLERANCES ARE:
DECIMALS
.XXX .125
.XXXX .050
BREAK EDGES .005/.020
FILLET RADIUS .005/.020

Top Plate, Mini TITLE

DO NOT SCALE DRAWING

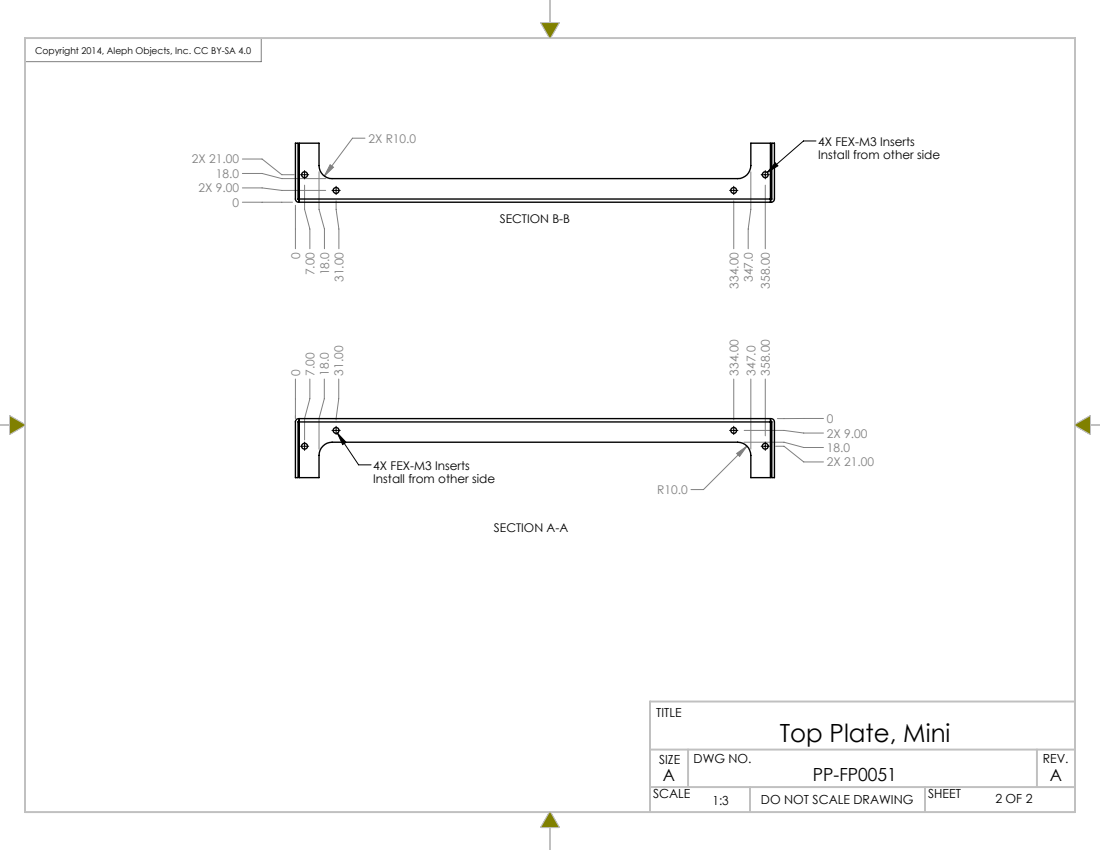
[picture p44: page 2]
SECTION A-A; SECTION B-B; SCALE; 2 OF 2 SHEET; DWG NO.; REV.

Copyright 2014, Aleph Objects, Inc. CC BY-SA 4.0

4X FEX-M3 Inserts
Install from other side

Top Plate, Mini
DO NOT SCALE DRAWING

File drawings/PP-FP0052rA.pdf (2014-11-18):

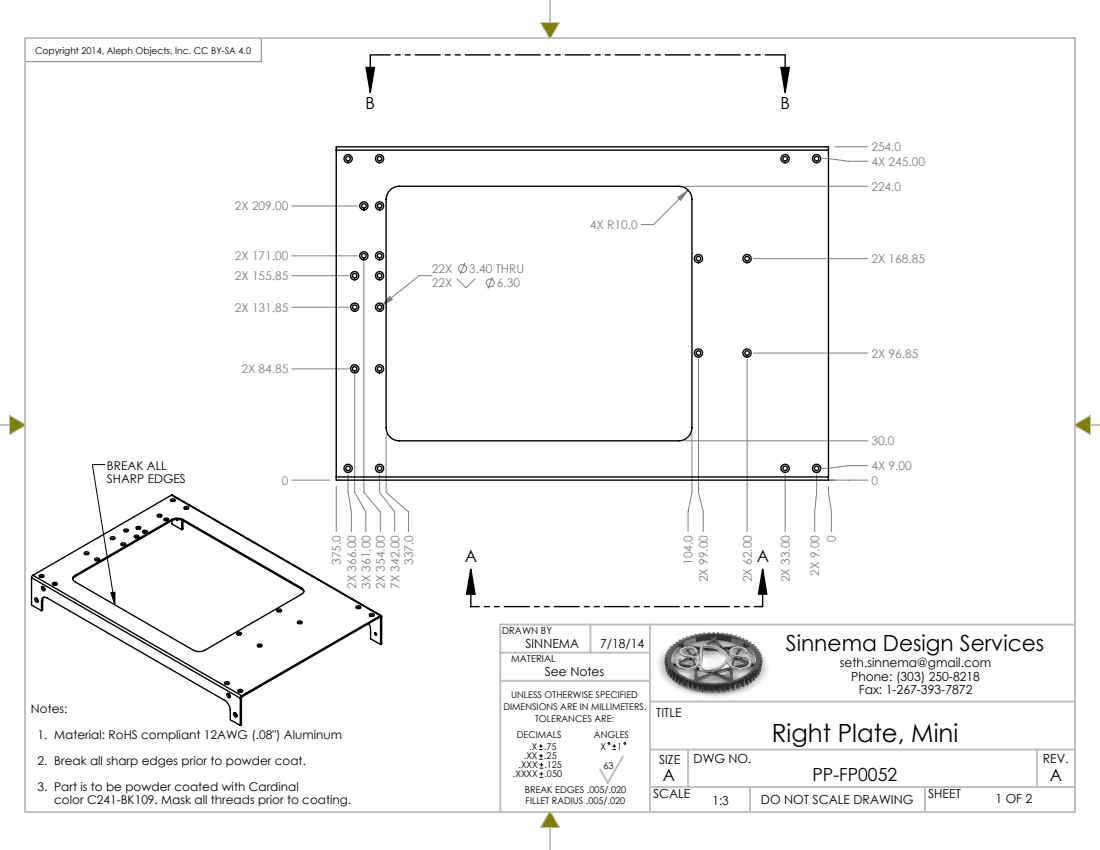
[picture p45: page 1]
22X 3.40 THRU; BREAK ALL SHARP EDGES; See Notes; DRAWN BY; SCALE; 1 OF 2 SHEET; DWG NO.; REV.

Copyright 2014, Aleph Objects, Inc. CC BY-SA 4.0

Sinnema Design Services

seth.sinnema@gmail.com
Phone: (303) 250-8218
Fax: 1-267-393-7872
Right Plate, Mini
DO NOT SCALE DRAWING

UNLESS OTHERWISE SPECIFIED
DIMENSIONS ARE IN MILLIMETERS.
TOLERANCES ARE:
DECIMALS
.XXX .125
.XXXX .050
BREAK EDGES .005/.020
FILLET RADIUS .005/.020

Notes:
1. Material: RoHS compliant 12AWG (.08") Aluminum
2. Break all sharp edges prior to powder coat.
3. Part is to be powder coated with Cardinal
color C241-BK109. Mask all threads prior to coating.

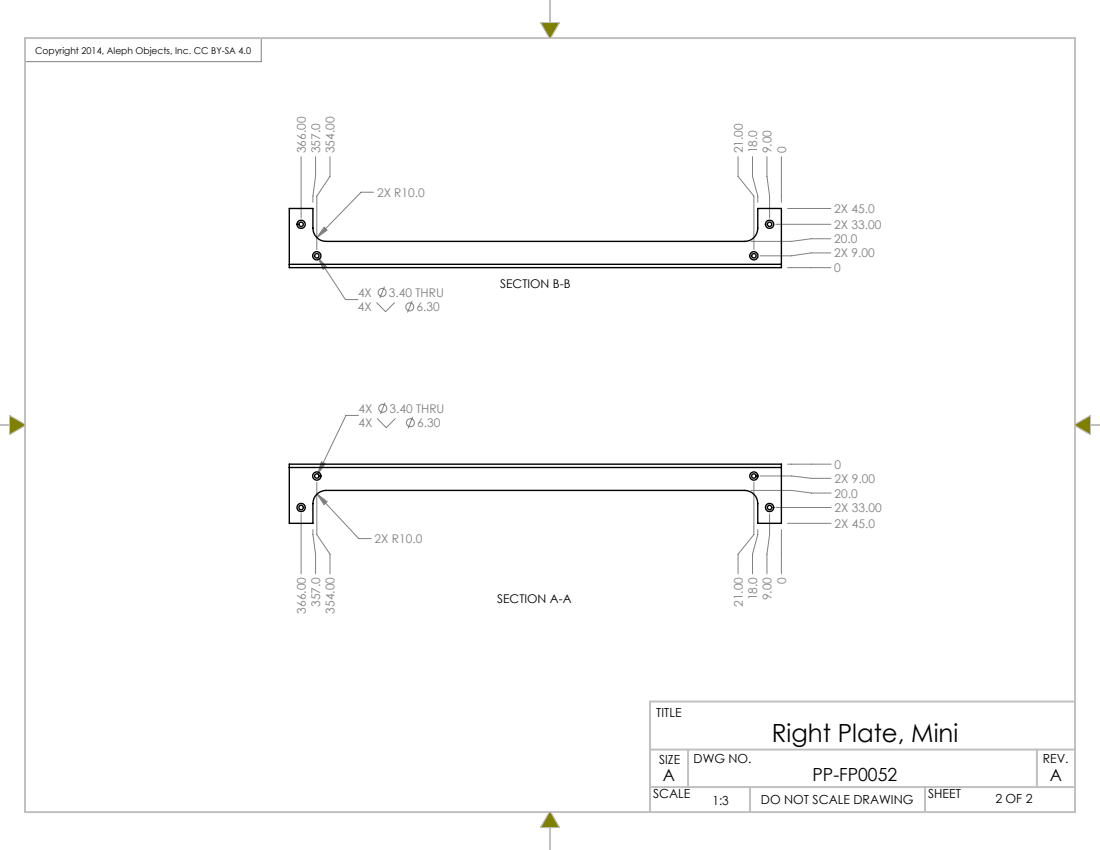
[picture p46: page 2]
4X 3.40 THRU; SECTION B-B; SECTION A-A; SCALE; 2 OF 2 SHEET; DWG NO.; REV.

Copyright 2014, Aleph Objects, Inc. CC BY-SA 4.0

Right Plate, Mini
DO NOT SCALE DRAWING

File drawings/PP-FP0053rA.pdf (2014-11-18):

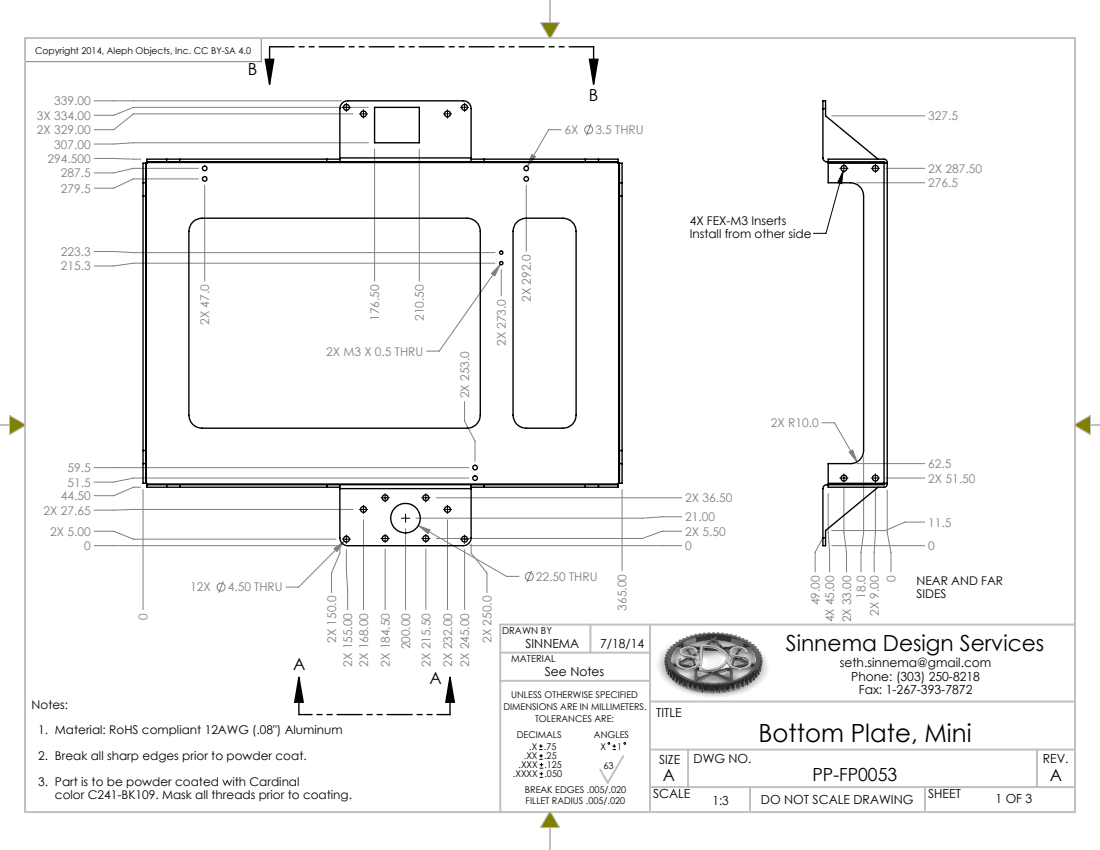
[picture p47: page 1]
12X 4.50 THRU; 22.50 THRU; 2X M3 X 0.5 THRU; 6X 3.5 THRU; See Notes; DRAWN BY; SCALE; 1 OF 3 SHEET; DWG NO.; REV.

Copyright 2014, Aleph Objects, Inc. CC BY-SA 4.0

4X FEX-M3 Inserts
Install from other side

Sinnema Design Services

NEAR AND FAR
SIDES

seth.sinnema@gmail.com
Phone: (303) 250-8218
Fax: 1-267-393-7872
Bottom Plate, Mini
DO NOT SCALE DRAWING

UNLESS OTHERWISE SPECIFIED
DIMENSIONS ARE IN MILLIMETERS.
TOLERANCES ARE:
DECIMALS
.XXX .125
.XXXX .050
BREAK EDGES .005/.020
FILLET RADIUS .005/.020

Notes:
1. Material: RoHS compliant 12AWG (.08") Aluminum
2. Break all sharp edges prior to powder coat.
3. Part is to be powder coated with Cardinal
color C241-BK109. Mask all threads prior to coating.

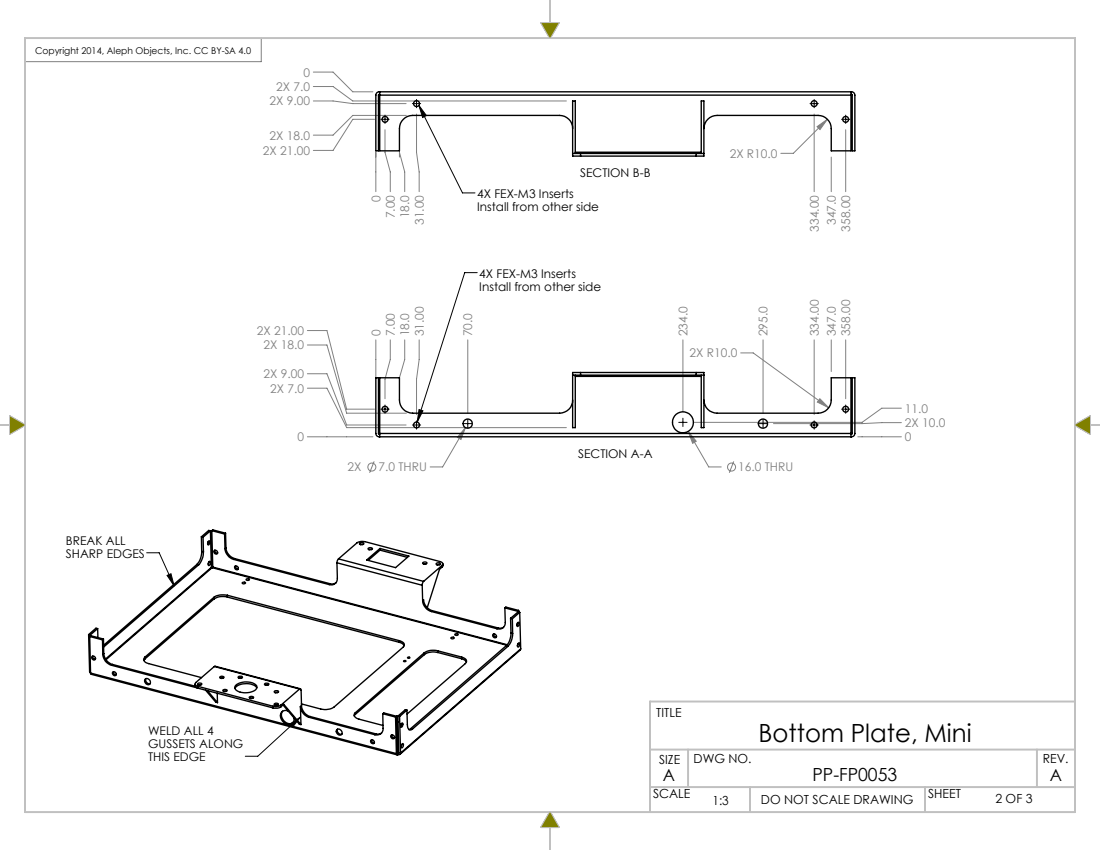
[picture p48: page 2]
WELD ALL 4 GUSSETS ALONG THIS EDGE; BREAK ALL SHARP EDGES; 2X 7.0 THRU; 16.0 THRU; SECTION A-A; SECTION B-B; SCALE; 2 OF 3 SHEET; DWG NO.; REV.

4X FEX-M3 Inserts
Install from other side

Bottom Plate, Mini

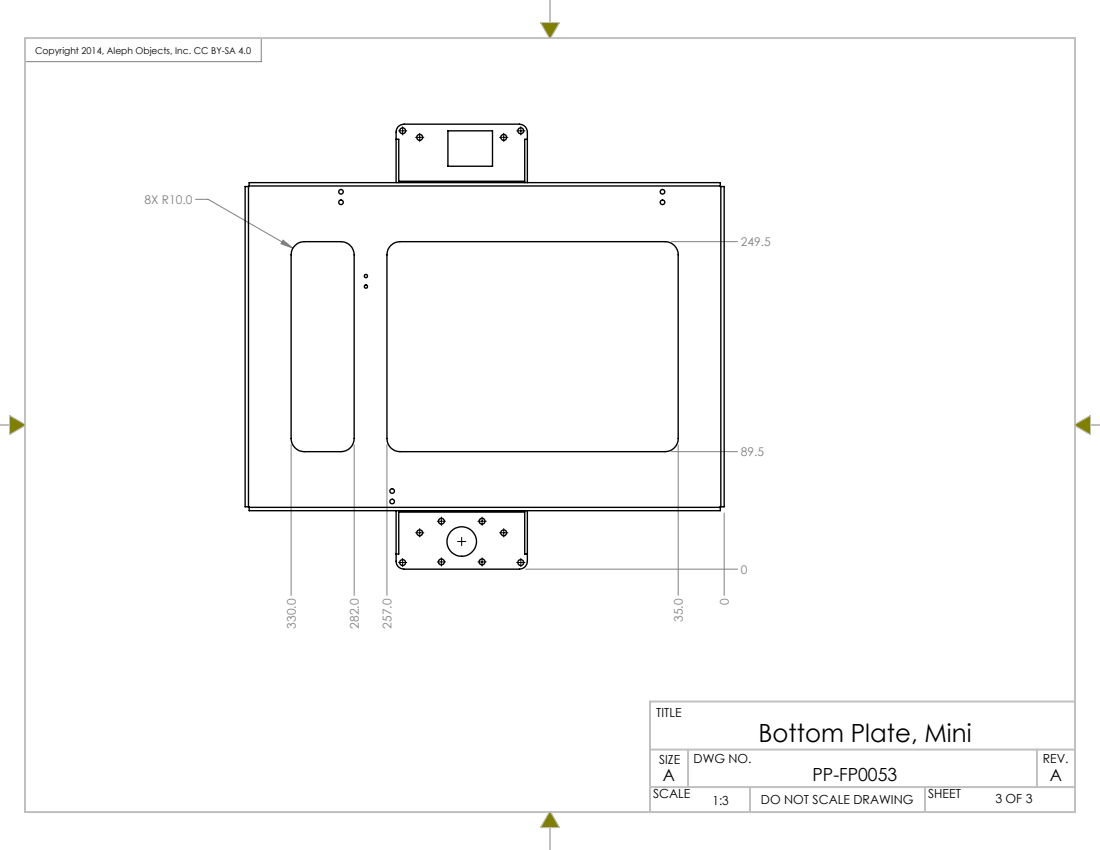
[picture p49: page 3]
SCALE; 3 OF 3 SHEET; DWG NO.; REV.

Bottom Plate, Mini

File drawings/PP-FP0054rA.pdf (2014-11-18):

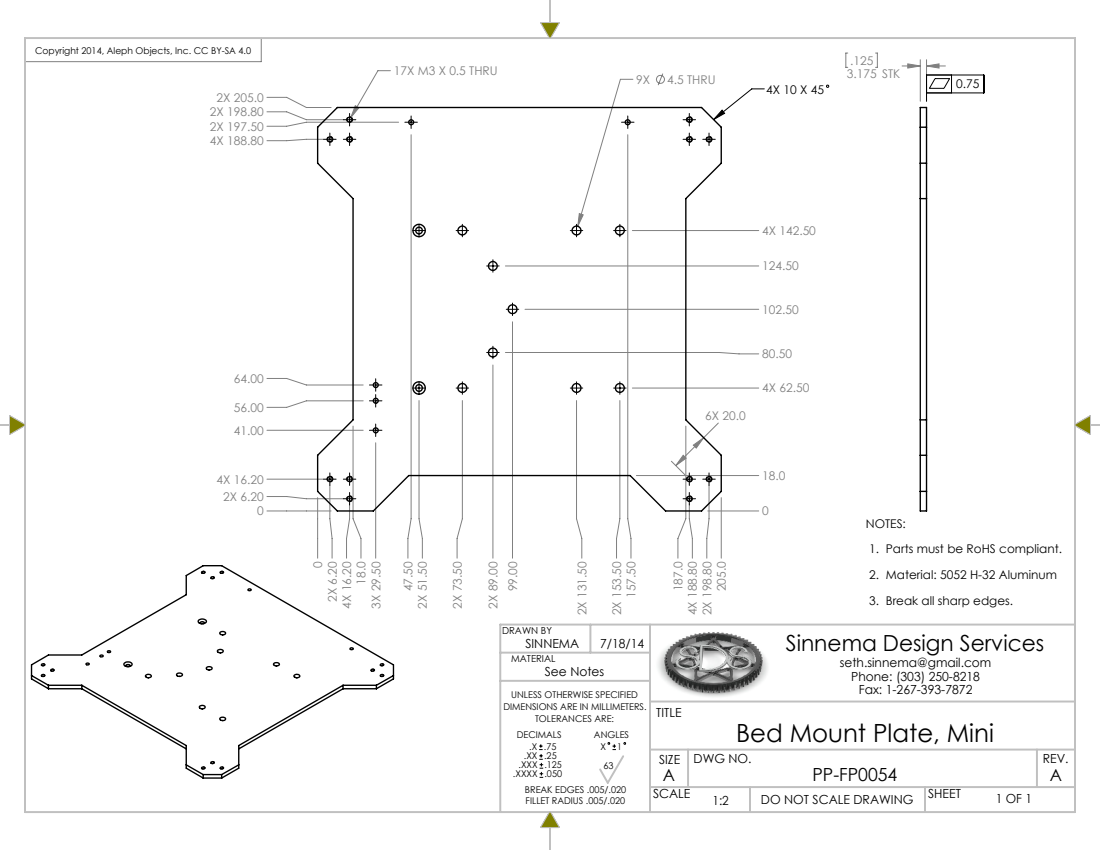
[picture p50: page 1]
17X M3 X 0.5 THRU; 9X 4.5 THRU; 3.175 STK; See Notes; DRAWN BY; SCALE; 1 OF 1 SHEET; DWG NO.; REV.

Copyright 2014, Aleph Objects, Inc. CC BY-SA 4.0

NOTES:
1. Parts must be RoHS compliant.
2. Material: 5052 H-32 Aluminum
3. Break all sharp edges.
Sinnema Design Services

seth.sinnema@gmail.com
Phone: (303) 250-8218
Fax: 1-267-393-7872

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

TITLE
Bed Mount Plate, Mini

DO NOT SCALE DRAWING

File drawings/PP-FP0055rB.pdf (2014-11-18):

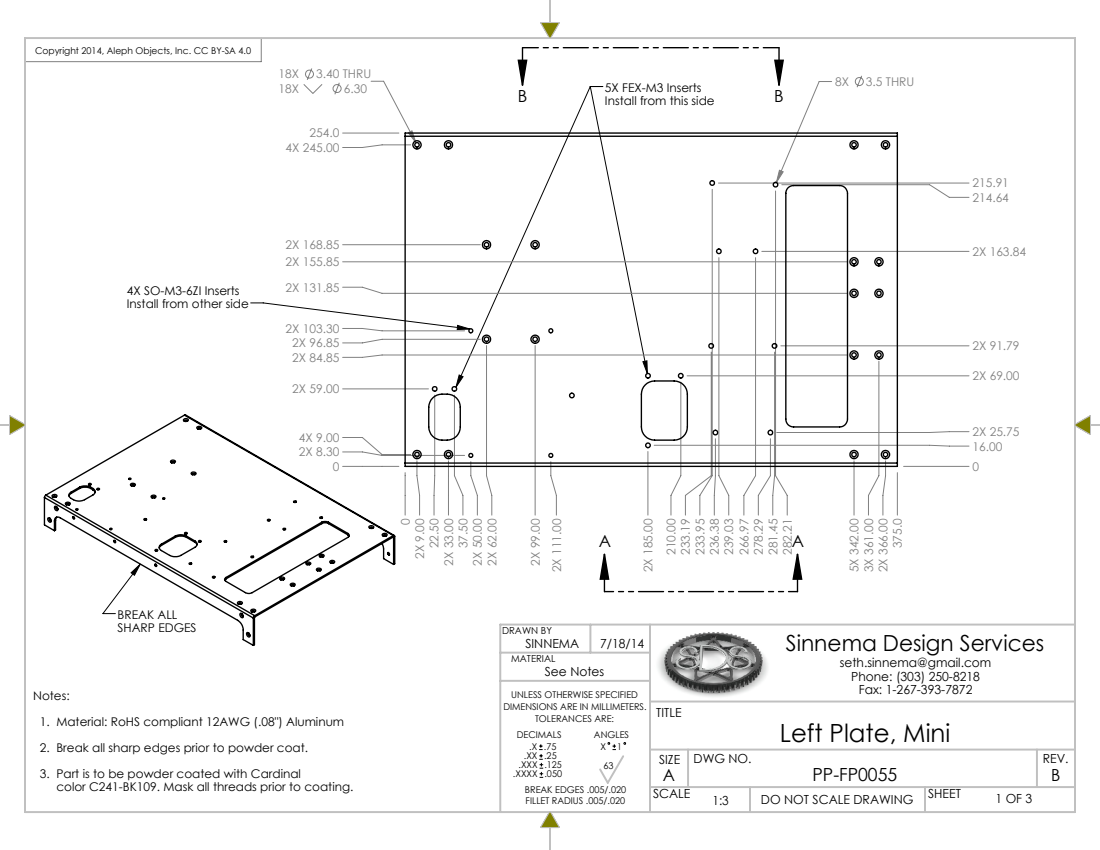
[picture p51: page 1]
18X 3.40 THRU; 8X 3.5 THRU 0 2X 9.00; B 5X FEX-M3 Inserts; BREAK ALL SHARP EDGES; See Notes; DRAWN BY; SCALE; 1 OF 3 SHEET; DWG NO.; REV.; Fax: 1-267-393-7872 Notes:

Copyright 2014, Aleph Objects, Inc. CC BY-SA 4.0

Install from this side

4X SO-M3-6ZI Inserts
Install from other side

Sinnema Design Services

seth.sinnema@gmail.com
Phone: (303) 250-8218
Left Plate, Mini
DO NOT SCALE DRAWING

UNLESS OTHERWISE SPECIFIED
DIMENSIONS ARE IN MILLIMETERS.
TOLERANCES ARE:
DECIMALS
.XXX .125
.XXXX .050
BREAK EDGES .005/.020
FILLET RADIUS .005/.020

1. Material: RoHS compliant 12AWG (.08") Aluminum
2. Break all sharp edges prior to powder coat.
3. Part is to be powder coated with Cardinal
color C241-BK109. Mask all threads prior to coating.

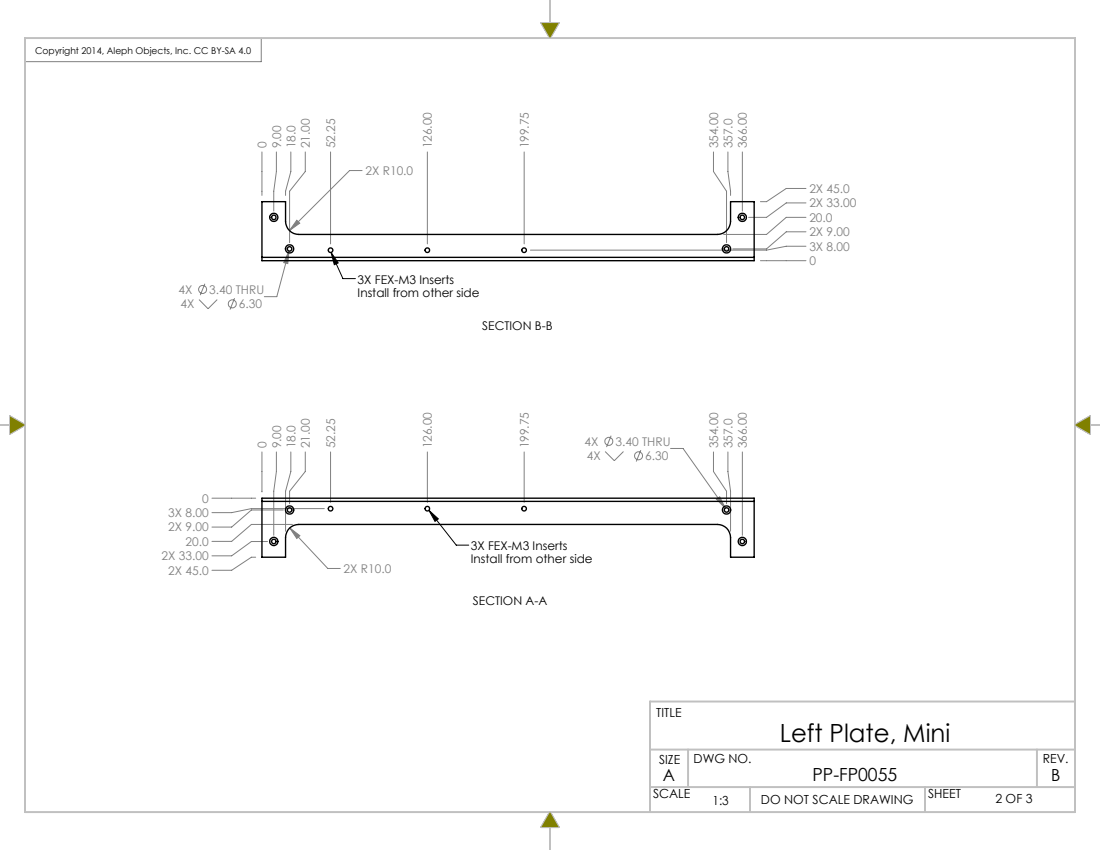
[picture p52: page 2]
4X 3.40 THRU; SECTION B-B; SECTION A-A; SCALE; 2 OF 3 SHEET; DWG NO.; REV.

3X FEX-M3 Inserts
Install from other side

Left Plate, Mini

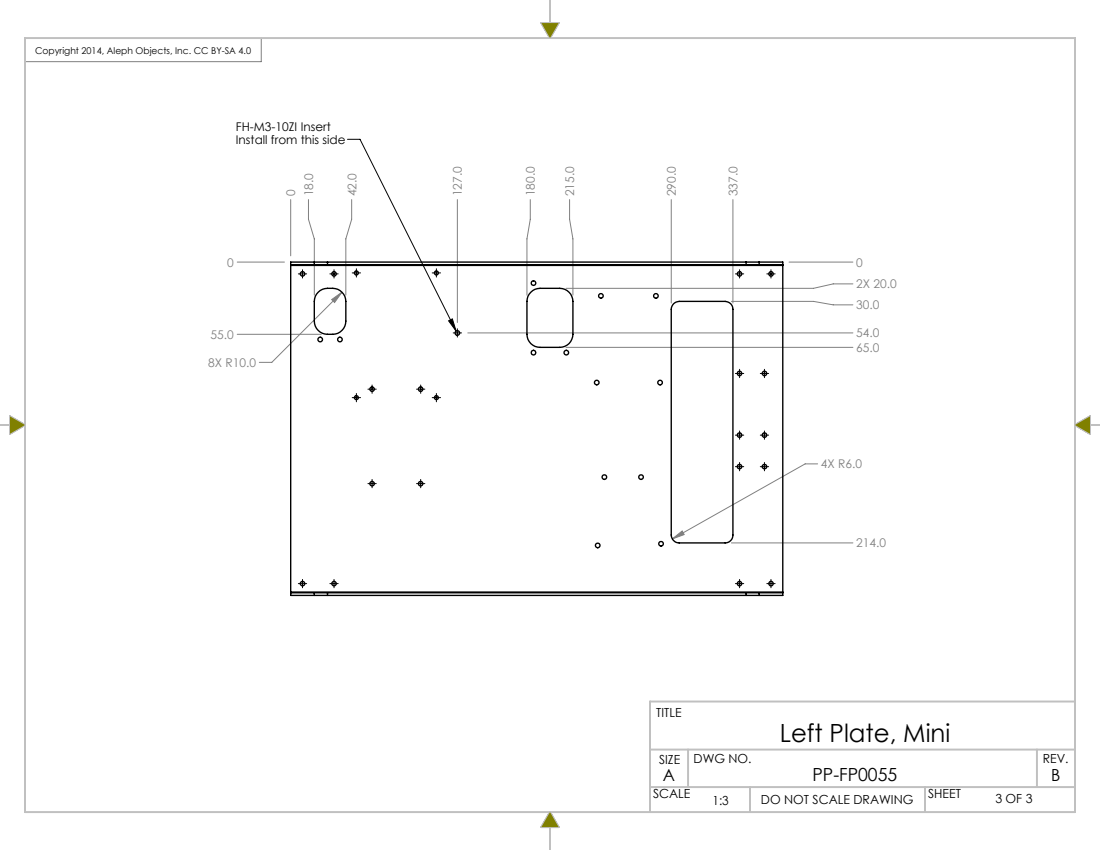
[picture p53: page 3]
SCALE; 3 OF 3 SHEET; DWG NO.; REV.

FH-M3-10ZI Insert
Install from this side

Left Plate, Mini

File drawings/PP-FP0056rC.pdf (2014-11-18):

R.FULL TYP; SEAM WELD 4X EDGES AND GRIND SMOOTH; SEE NOTES; DRAWN BY; SCALE; 1 OF 2 SHEET; DWG NO.; REV.

Copyright 2014, Aleph Objects, Inc. CC BY-SA 4.0

Notes:
1. Material: RoHS compliant 12AWG (.08") Aluminum
2. Break all sharp edges prior to powder coat.
3. Part is to be powder coated with Cardinal
color C241-BK109. Mask all threads prior to coating.
Sinnema Design Services

seth.sinnema@gmail.com
Phone: (303) 250-8218
Fax: 1-267-393-7872

UNLESS OTHERWISE SPECIFIED
DIMENSIONS ARE IN MILLIMETERS.
TOLERANCES ARE:
DECIMALS
.XXX .125
.XXXX .050
BREAK EDGES .005/.020
FILLET RADIUS .005/.020

TITLE
Electronics Case, Mini

DO NOT SCALE DRAWING

3X 3.40 THRU; R.FULL TYP; SECTION A-A; 6.0 THRU 0 155.30; 8X 3.40 THRU; SECTION C-C; SCALE; 2 OF 2 SHEET; DWG NO.; REV.

Copyright 2014, Aleph Objects, Inc. CC BY-SA 4.0

2X FEX-M3 Inserts
Install from other side

FH-M3-10ZI Insert
Install from this side

SECTION B-B
Electronics Case, Mini

DO NOT SCALE DRAWING


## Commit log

2014-07-15 Initial setup of LulzBot Easy TAZ Mini Developer's Guide.
    new file: .gitignore
    new file: Colophon.tex
    new file: Contact.tex
    new file: Copyright.tex
    new file: EZDEV-thumbnail.tex
    new file: EZDEV.gst
    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
2014-09-13 Change Easy TAZ Mini to LulzBot Mini and update URLs.
    modified: Colophon.tex
    modified: Contact.tex
    modified: Controller.tex
    modified: Copyright.tex
    modified: Electrical.tex
    modified: Introduction.tex
    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
2014-11-18 Add LulzBot Mini Bill of Materials (Daffodil).
    modified: Mechanical.tex
    new file: docs/daffodil_bom.pdf
    modified: mini-dev-thumbnail.pdf
    modified: mini-dev.pdf
    modified: mini-dev.tex
2014-11-18 Add Wire Harness List doc.
    modified: Packing.tex
    modified: QA.tex
    modified: docs/packlist.pdf
    modified: docs/qa.pdf
    new file: docs/wire-harness-list.pdf
    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
2014-11-18 Add mechanical drawings.
    renamed: docs/daffodil_bom.pdf -> docs/bom.pdf
    new file: drawings/PP-FP0051rA.pdf
    new file: drawings/PP-FP0052rA.pdf
    new file: drawings/PP-FP0053rA.pdf
    new file: drawings/PP-FP0054rA.pdf
    new file: drawings/PP-FP0055rB.pdf
    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
2014-11-18 Add STLs and PNGs of printed parts (Daffodil).
    new file: STL/bedcorner.stl
    new file: STL/bedcorner.stl.png
    new file: STL/beltmount.stl
    new file: STL/beltmount.stl.png
    new file: STL/doublebearingholder.stl
    new file: STL/doublebearingholder.stl.png
    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
    [bedcorner.stl, beltmount.stl, doublebearingholder.stl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]
